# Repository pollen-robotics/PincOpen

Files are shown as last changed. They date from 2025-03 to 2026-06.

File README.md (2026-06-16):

[][cc-by-sa]

This work is licensed under a
[Creative Commons Attribution-ShareAlike 4.0 International License][cc-by-sa].

[][cc-by-sa]

[cc-by-sa]: http://creativecommons.org/licenses/by-sa/4.0/
[cc-by-sa-image]: https://licensebuttons.net/l/by-sa/4.0/88x31.png
[cc-by-sa-shield]: https://img.shields.io/badge/License-CC%20BY--SA%204.0-lightgrey.svg

Watch the video (https://www.youtube.com/shorts/5o2Au9_xjNQ)

# Pinc'Open project
[Pinc'Open](https://github.com/pollen-robotics/PincOpen/tree/main) is a low-cost (~25€) and open-source parallel-finger gripper, derived from [Pollen Robotics Reachy 2](https://www.pollen-robotics.com/reachy/)'s gripper

## Table of contents

- [Pinc'Open Presentation](#pincopen-project)
    - [What is Pinc'Open](#what-is-pincopen)
    - [Reachy 2 "Pincette" gripper](#reachy-2-pincette-gripper)
    - [Areas of focus](#areas-of-focus)
- [Build Resources](#build-resources)
    - [BOM (Bill Of Materials)](#bom-bill-of-materials)
    - [STL Files and Onshape document](#stl-files-and-onshape-document)
    - [Configure the motor before assembly](#configure-the-motor-before-assembly)
    - [Assembly Guide](#assembly-guide)
    - [How to flash and test the gripper](#how-to-flash-and-test-the-gripper)
- [Project Updates & Community](#project-updates--community)
    - [Updates history](#updates-history)
    - [Project posts](#project-posts)
    - [To Do List](#to-do-list)
    - [FAQ](#faq)
    - [Contact](#contact)
    - [Thank you](#thank-you)

## What is Pinc'Open?
The aim of this project is to make robotic manipulation more accessible, so that anyone with an idea but not the budget can make advances in this field possible.  
The quality of movement, mechanical strength and precision may not be as good as an industrial product, but a 2-finger parallel robotic gripper can be built for less than 25€! And we'll see that the performance is still good.  
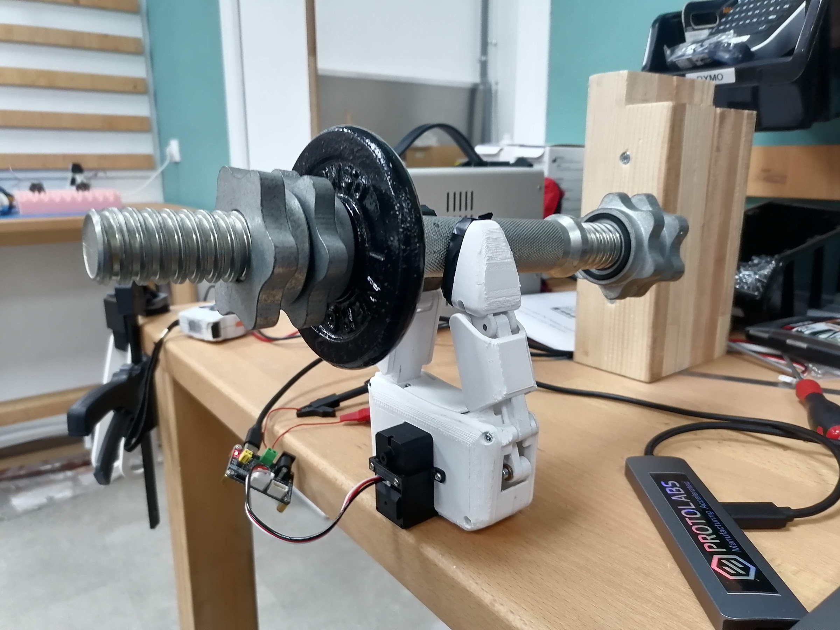
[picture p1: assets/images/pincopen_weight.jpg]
PincOpen_weight


The secondary goal is to make this gripper compatible with the [SO-ARM100](https://github.com/TheRobotStudio/SO-ARM100) open-source arm, so that the same motor as the current gripper can be used on our Pinc'Open. So the 25€ includes a motor that is already included in the $100 of the SO-ARM100.

What's more, the tip is interchangeable! That way, you can fit exactly what you need for your particular application.  
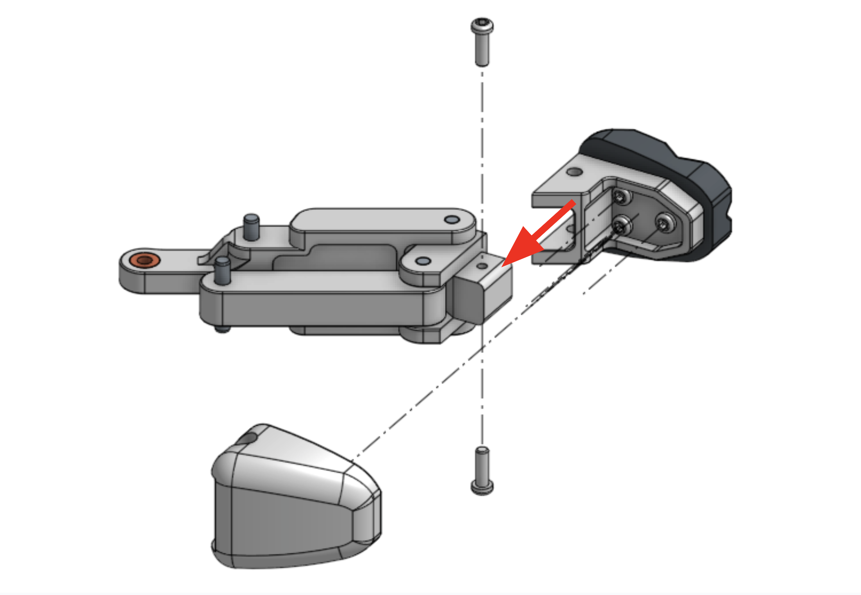
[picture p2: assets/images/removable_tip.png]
removable_tip


## Reachy 2 "Pincette" gripper
The Pincette v1.0 gripper, released at the same time as [Reachy 2](https://www.pollen-robotics.com/reachy/), is a two-parallel-finger hand designed for versatility and accurate, strong grasping.  
Pincette
Joints are based on high-quality standard components, and mechanical parts are machined from metal for greater rigidity and precision.  
However, these qualities come at a considerable cost: today, for just a few units manufactured, the BOM costs ~€1,700 per unit.  

This is acceptable depending on the application, but not for those who want to build a low-cost robotic gripper.

## Areas of focus:
- Make every mechanical custom part 3D printable, and not easily breakable, to avoid expensive metal machining.
- Change the expensive [Robotis Dynamixel motor](https://emanual.robotis.com/docs/en/dxl/x/xm430-w210/) to a cheap [Feetech STS3215](https://www.feetechrc.com/525603.html) motor.
- Remove all the high-quality but expensive standard components and find mechanical tricks to replace them.
- Find a trick to imitate a torque limitation while using position control on a motor that doesn't have this feature. Otherwise, the motor burns (or turns off thanks to security) or the plastic mechanical part can break...

# Build Resources
## BOM (Bill Of Materials)
The list of all needed components is available here:  
[PincOpen BOM](https://docs.google.com/spreadsheets/d/1iEKxfsqo3RnKw0QtdLJ2hEtYNDy2LInxrnCFLAhpxHk/edit?usp=sharing)  

There is the standalone PincOpen gripper BOM (~25€), then optional components like the interface with the [SO-ARM100](https://github.com/TheRobotStudio/SO-ARM100) project, or a Realsense camera stand for example.

## STL Files and Onshape document
STL and Steps files can be found [here](https://github.com/pollen-robotics/PincOpen/tree/main/cad)  

Everyone can access the Onshape document too:   
[Link Onshape](https://cad.onshape.com/documents/96518c699fd03eea508b06d3/w/d5f95a6266b027d84ae48634/e/e41e675b82a4f671f01336e0)  
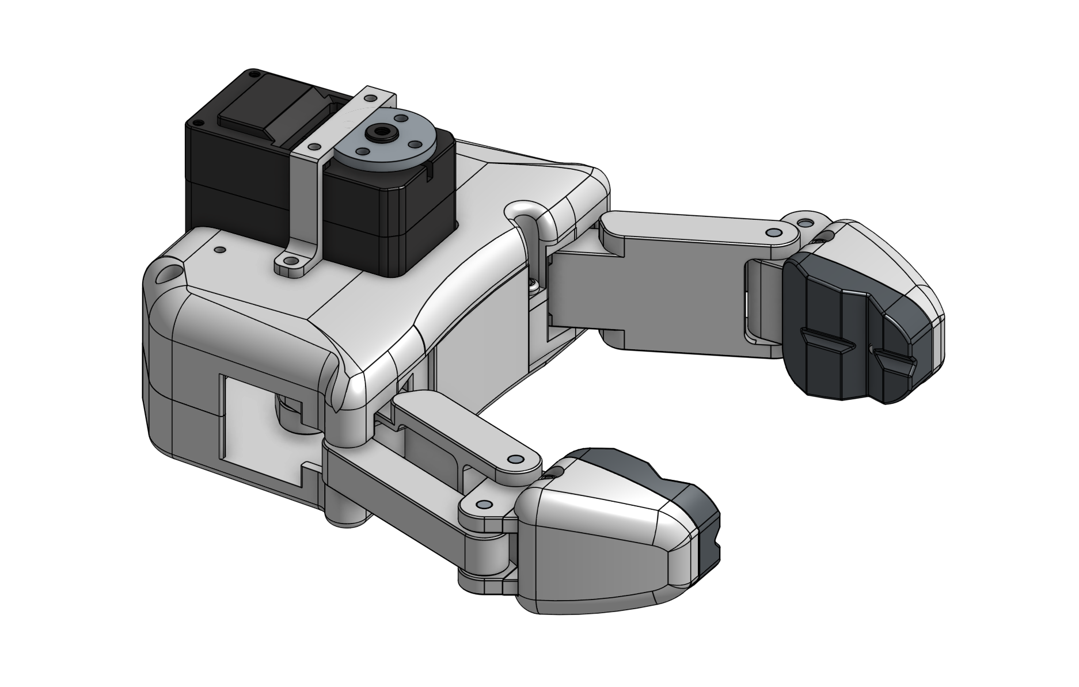
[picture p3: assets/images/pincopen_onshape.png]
pincopen onshape picture
  

Note that you can set a configuration in the assembly, like the default assembly, or with the interface part for SO-ARM100, or the configuration for camera mounting.

## Configure the motor before assembly
To configure the motor as it should be, please first clone & install [Lerobot library](https://github.com/huggingface/lerobot/tree/main).

Then connect and power up your motor, and run the following command: 

```bash
python lerobot/scripts/configure_motor.py --port /dev/ttyACM0 --brand feetech --model sts3215 --baudrate 1000000 --ID <ID>
```

Make sure to replace the port with your USB serial port and the ID with "6".

## Assembly Guide
Here is an assembly guide to explain how to print all the needed custom parts and how to use them to build this gripper.  
[=> Assembly Guide](/docs/PincOpen_Assembly_Instructions.pdf)  
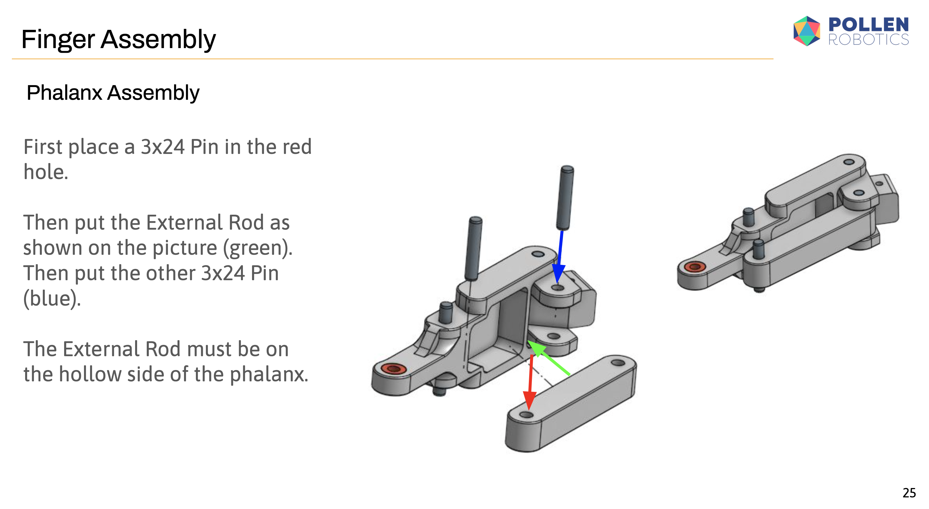
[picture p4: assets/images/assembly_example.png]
Assembly Example
  

There is also a guide about how to build an Intel Realsense D405 camera mount here:  
[=> Camera Mount Assembly](/docs/camera_mount_assemby.md)

## How to flash and test the gripper
First of all, please install the pypot library, updated with the Feetech motors:  
https://github.com/pollen-robotics/pypot/tree/support-feetech-sts3215  

Then, please refer to the [flash&test notebook](https://github.com/pollen-robotics/PincOpen/tree/main/flash_and_tests)

# Project Updates & Community
## Updates history
[Updates history](/docs/changelog.md)  

## Community projects
- ROS2 PincOpen Driver - School of Engineering and Computing, Christopher Newport University - [[Github](https://github.com/CNURobotics/pinc_open_driver)]. 
- MuJoCo Simulation Support (PR) - [[Github](https://github.com/pollen-robotics/PincOpen/pull/6)] 
- ICRA 2026 Smart grasping using embedded 3D force (tactile) sensing from Melexis - Milan Amighi, Constantin Scholz and Bram Vanderborght (Brubotics - VUB & imec), in collaboration with Melexis - [[Tutorial Website](https://mech.vub.ac.be/multibody/ICRA_conference_workshop.htm)]
- [Mobile Manipulation with LeKiwi and PincOpen](https://huggingface.co/blog/zuoxingdong/mobile-manipulation-lekiwi-pincopen) - Xingdong Zuo - [[Github](https://github.com/zuoxingdong/lerobot-lekiwi)]

## To Do List
- Video showing the advantages of this more complex mechanism
- Technical explanation about how it was designed
- New camera mounting supports

## Project posts
- [Fingertips for better grip](/docs/grip_tip.md)
- [Mobile Manipulation with LeKiwi and PincOpen](https://huggingface.co/blog/zuoxingdong/mobile-manipulation-lekiwi-pincopen) - Xingdong Zuo - [[Github](https://github.com/zuoxingdong/lerobot-lekiwi)]

## FAQ
WIP

## Contact
[Contact me or Pollen Robotics](/docs/contact.md)

## Thank you
Huge thanks to those who have contributed to this project so far:
- [Antoine Pirrone](https://github.com/apirrone) for making great demos, all the advice and feedback
- [Pierre Rouanet](https://github.com/pierre-rouanet) for Feetech motors integration in pypot  
- [Jeremy Laville](https://www.linkedin.com/in/jeremy-laville-1038b176/) & [Matthieu Lapeyre](https://www.linkedin.com/in/matthieulapeyre/) for mechanical advice and original Reachy 2 Pincette co-development

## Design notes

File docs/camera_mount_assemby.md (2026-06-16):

# On-wrist Camera Mount Assembly

1. With a soldering iron, place 2x M3 inserts here:
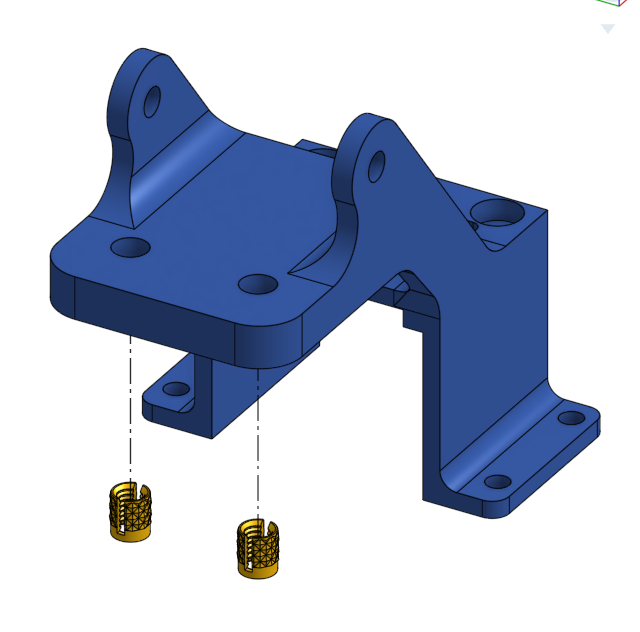
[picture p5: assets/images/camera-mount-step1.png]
Step 1
 

2. Then place 2x M3x25 screws here, used to adjust the angle of the camera, plus 2 nuts to lock the screw positions:
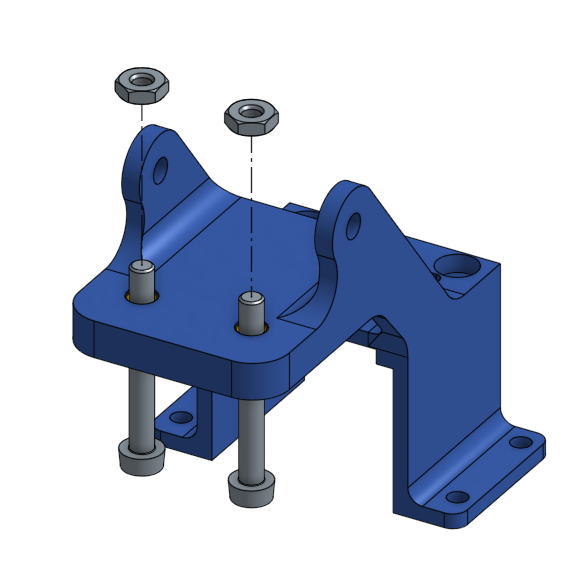
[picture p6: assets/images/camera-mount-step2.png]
Step 2


3. Put the mobile support in the base and secure the axis with two self-tapping 3x8mm screws (thermoplastic screws):
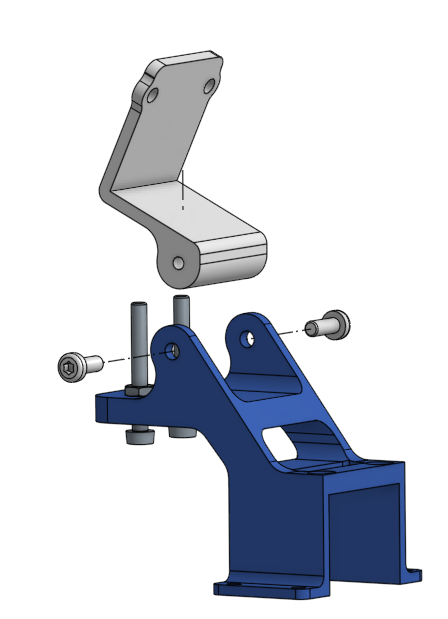
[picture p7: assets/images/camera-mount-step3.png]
Step 3


4. Then place the camera's back holes in front of the holes of the mobile support part and put in 2x M3x6 screws:
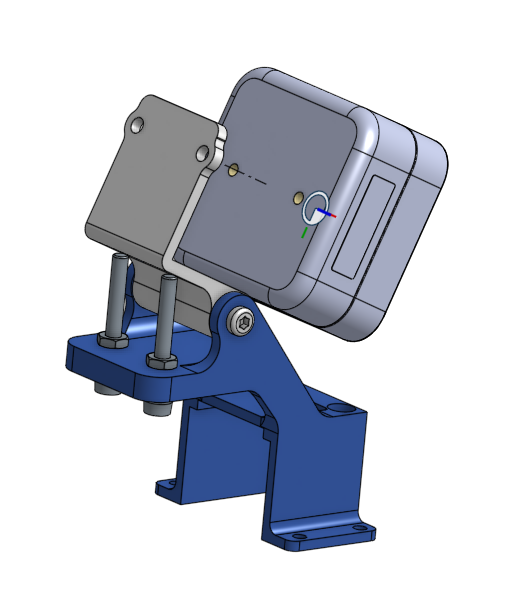
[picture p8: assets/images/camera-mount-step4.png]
Step 4


5. Put in 4x self-tapping 2.5x6mm screws:
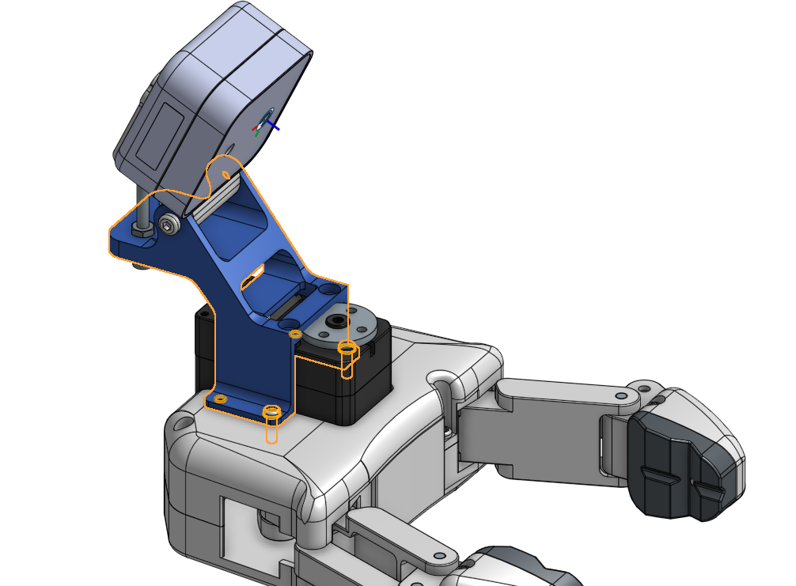
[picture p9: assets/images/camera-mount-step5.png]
Step 5


*Thanks to [Xingdong Zuo](https://github.com/zuoxingdong) for the contribution of this camera mount assembly guide.*

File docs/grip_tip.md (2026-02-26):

## Fingertips for Better Grip

We've added a small but useful feature to the fingertip design in the [Onshape model](https://cad.onshape.com/documents/96518c699fd03eea508b06d3/w/d5f95a6266b027d84ae48634/e/e41e675b82a4f671f01336e0), making it easier to improve grip performance.

### Flat Tip Design for Adhesive Grip Layers

The tip of the finger can be **flattened**, allowing you to:
- Cut the same shape from the **adhesive or anti-slip material** of your choice
- Stick it onto the fingertip
- **Fold the side flaps** neatly around the edges

To secure the folded flaps in place, you can add a **thin strip of tape or band** around the perimeter of the tip. This helps maintain a clean and durable finish.

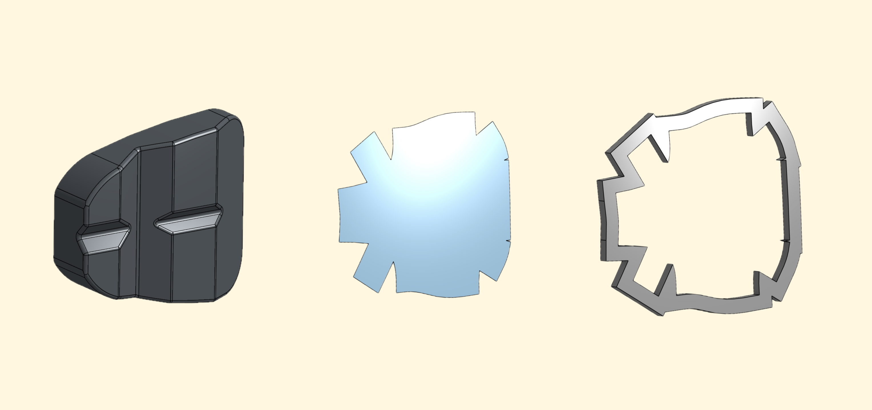
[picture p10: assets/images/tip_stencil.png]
tip_stencil


### Best Performing Material So Far: **3M GM400**

After testing various grip-enhancing materials, our favorite so far is the **3M GM400**

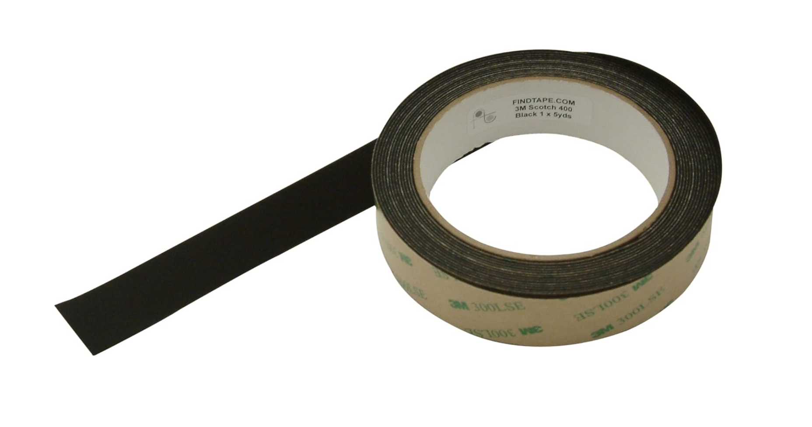
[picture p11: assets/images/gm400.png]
gm400


- Strong **dry adhesion** (not sticky, but highly grippy)
- Excellent **friction**, even on smooth objects
- Durable and **wear-resistant**, sticks well
- Easy to cut and apply

However, the cost is quite high and the quantity is probably too much for just covering one gripper tip...

> ⚠️ _Note: We have **no affiliation with 3M** — this is an objective recommendation based on hands-on testing._

### TPU Option – Deformable but Solid

You can also 3D print the fingertips in **TPU** with a **moderate infill (30–50%)**, resulting in:
- A flexible structure that adapts to object shapes
- Enough rigidity to preserve form and control

Combining TPU with an adhesive grip layer offers a great balance between **compliance and friction**.

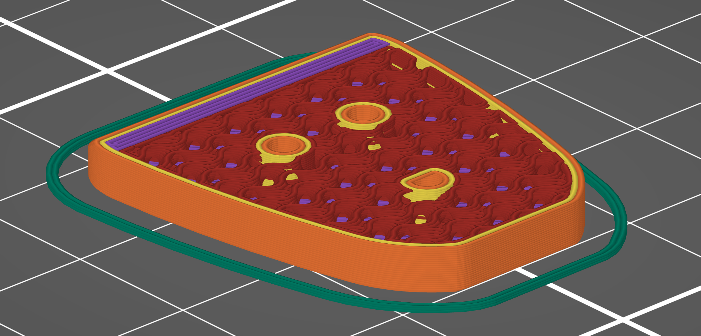
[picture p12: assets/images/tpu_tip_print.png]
tpu_tip


### Personal Preference: Rigid Base + Grip Layer

While TPU works well, **our personal preference** is to use a **rigid tip (PLA or PETG)** and simply add a **thin rubber-like or anti-slip layer** (such as GM400) on top.  
This approach avoids unwanted deformation, while still ensuring **strong and reliable grip** — especially useful when precise, repeatable grasps are needed.

Feel free to experiment with different grip materials — the flat tip shape makes it easy to try out and swap alternatives depending on your use case or your budget.

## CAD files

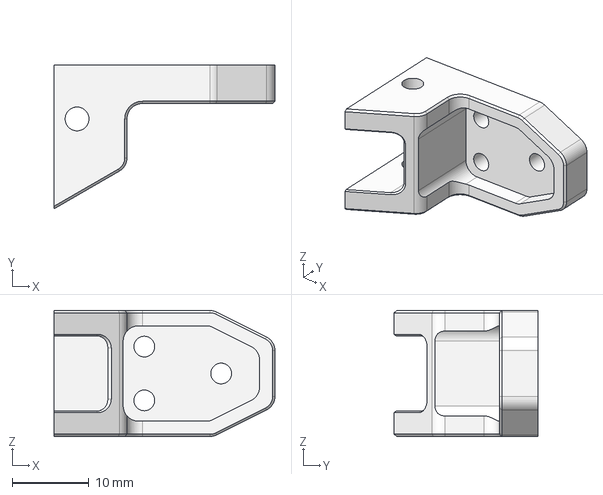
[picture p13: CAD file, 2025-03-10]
cad/step/Removable_Tip.step
28.8 x 18.7 x 16.4 mm

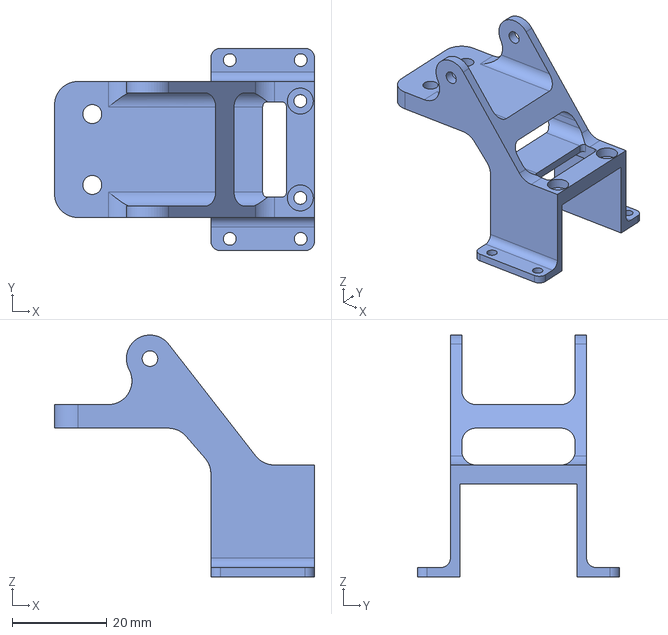
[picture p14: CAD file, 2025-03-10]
cad/step/Camera_basement.step
55.0 x 42.8 x 51.2 mm

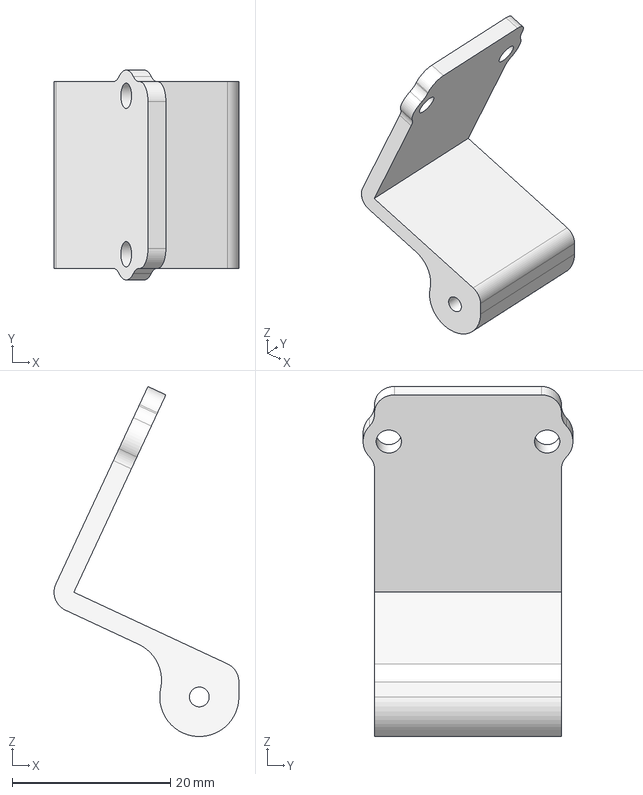
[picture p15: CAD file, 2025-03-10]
cad/step/Camera_mobile_sup.step
23.3 x 26.5 x 44.2 mm

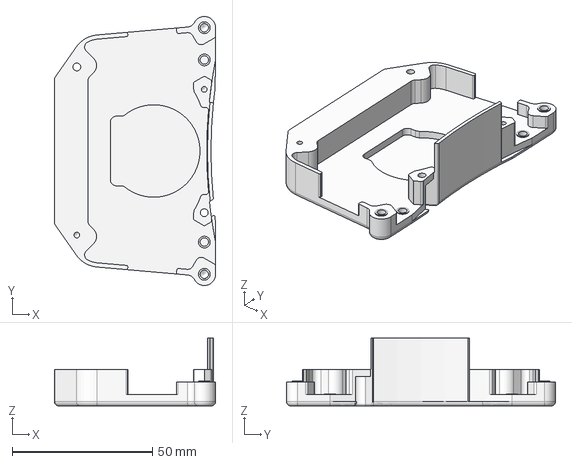
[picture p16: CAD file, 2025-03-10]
cad/step/Bottom_Plate.step
57.5 x 96.0 x 24.2 mm

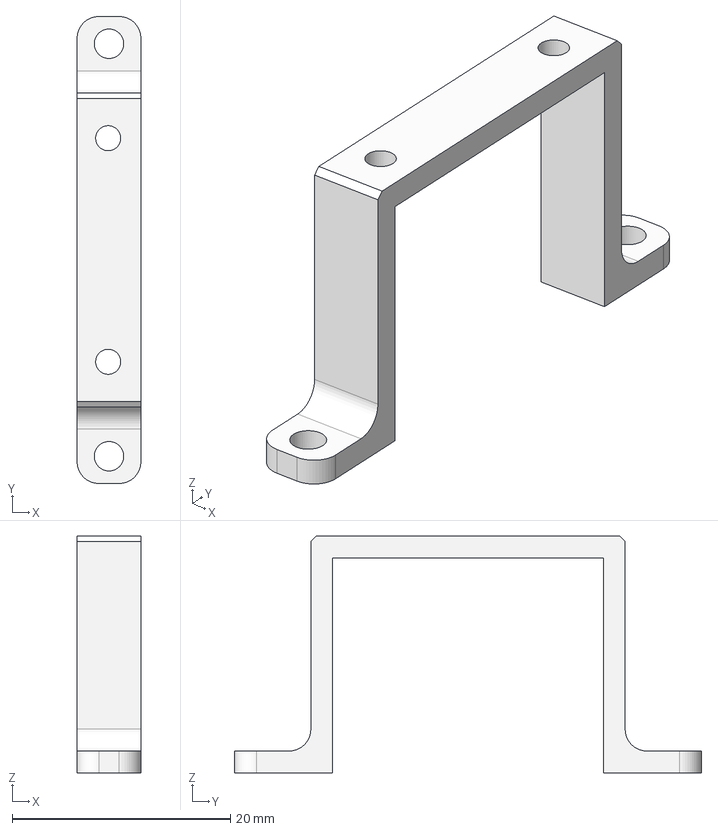
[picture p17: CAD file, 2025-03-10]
cad/step/Motor_Flange.step
5.85 x 42.8 x 21.7 mm

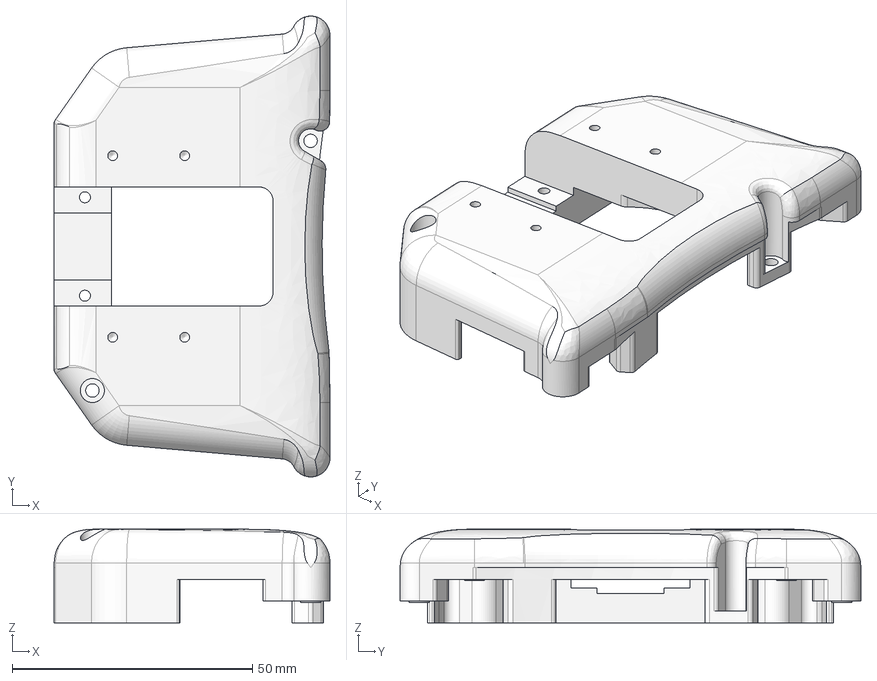
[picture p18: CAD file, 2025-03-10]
cad/step/Top_Plate.step
57.5 x 96.0 x 19.5 mm

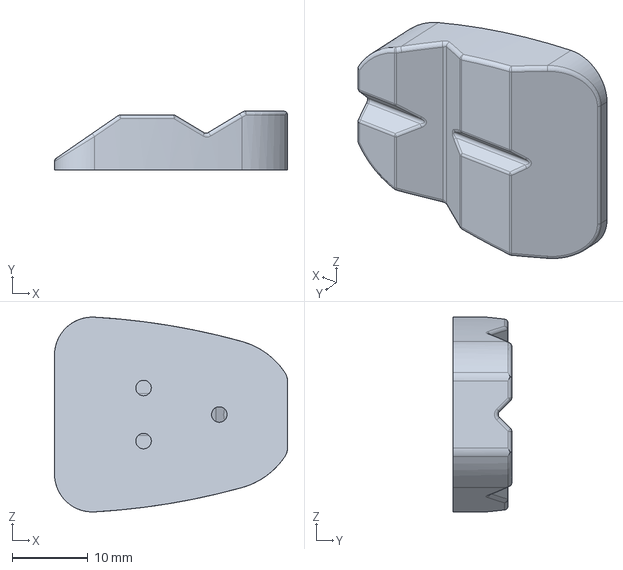
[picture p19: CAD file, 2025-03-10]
cad/step/Tip_Support.step
30.8 x 7.75 x 25.7 mm

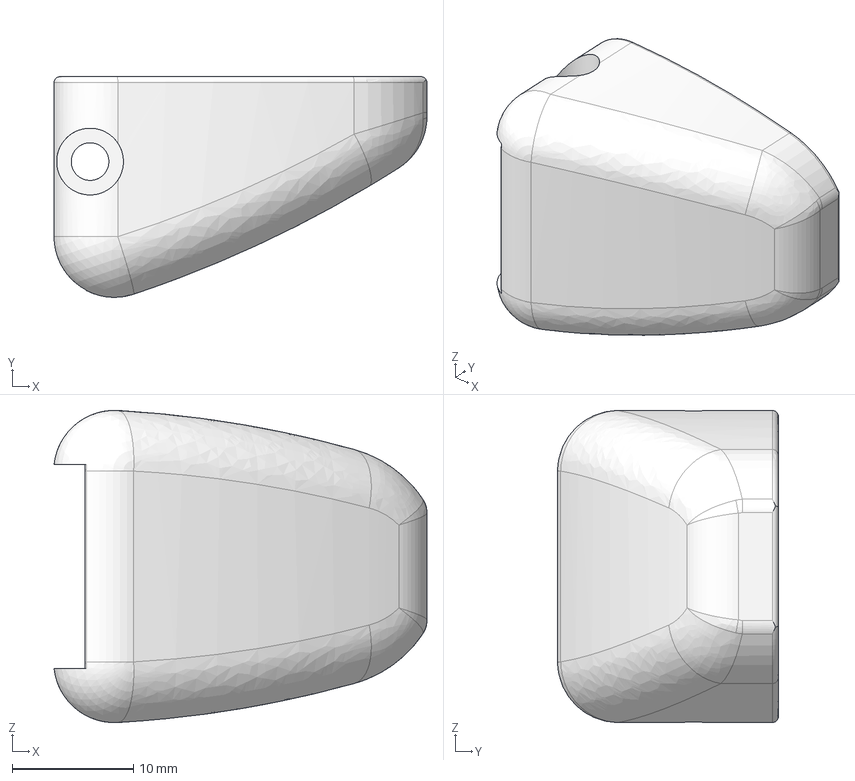
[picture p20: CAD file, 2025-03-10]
cad/step/Distal_Shell.step
30.7 x 18.2 x 25.7 mm

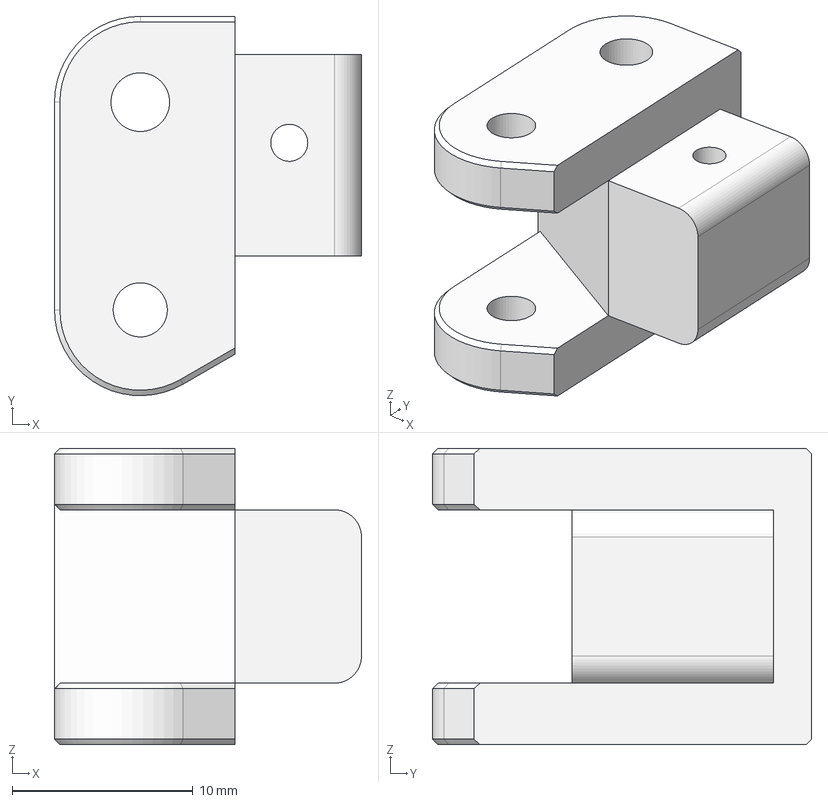
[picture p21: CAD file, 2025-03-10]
cad/step/Distal_Rod.step
17.0 x 21.0 x 16.4 mm

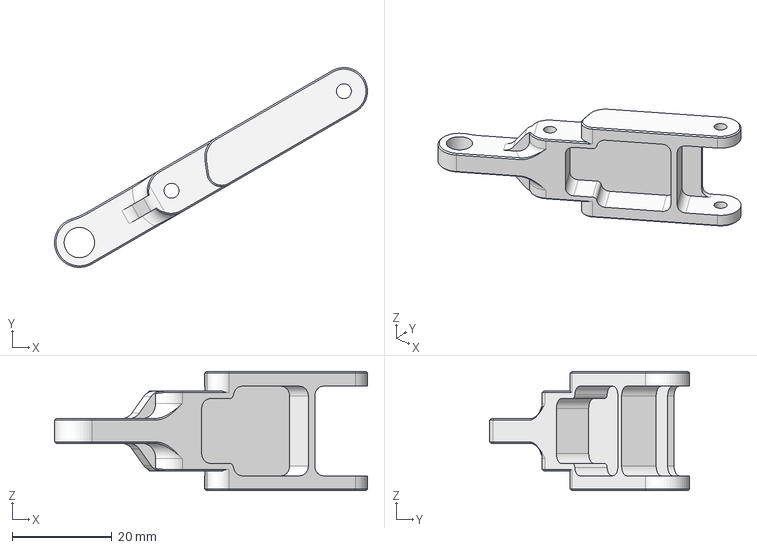
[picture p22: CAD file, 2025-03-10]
cad/step/Internal_Rod.step
62.9 x 40.2 x 24.0 mm

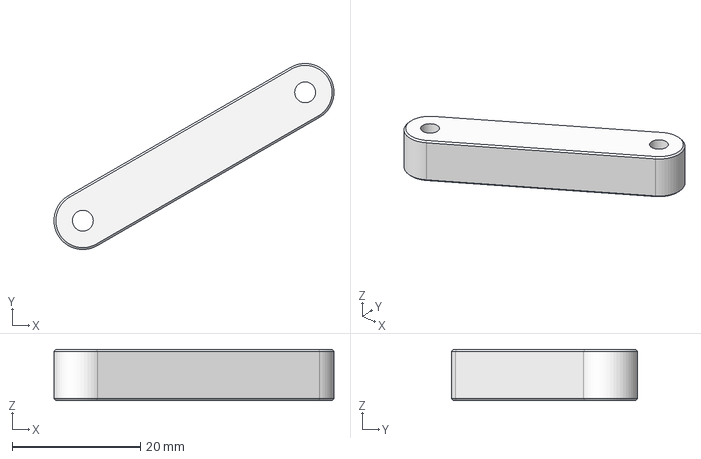
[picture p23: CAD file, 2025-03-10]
cad/step/External_Rod.step
43.6 x 29.0 x 8.00 mm

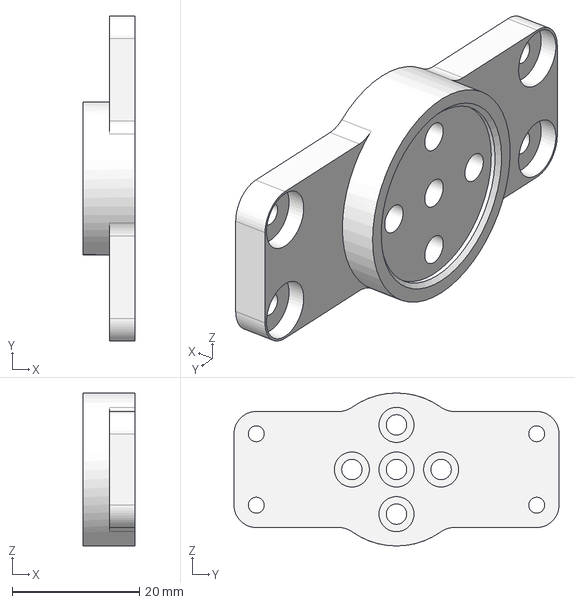
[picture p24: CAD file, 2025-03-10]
cad/step/Interface_ARM100.step
8.12 x 51.0 x 24.0 mm

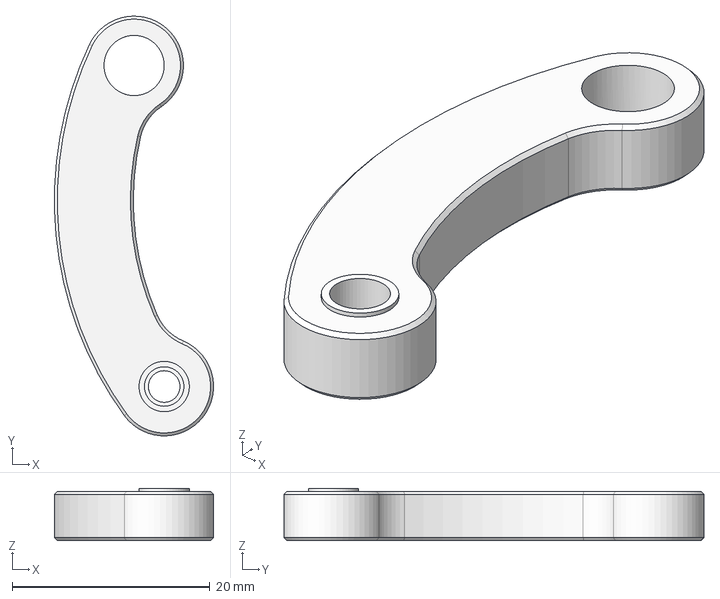
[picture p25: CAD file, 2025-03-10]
cad/step/Driving_Rod.step
16.1 x 42.5 x 5.30 mm

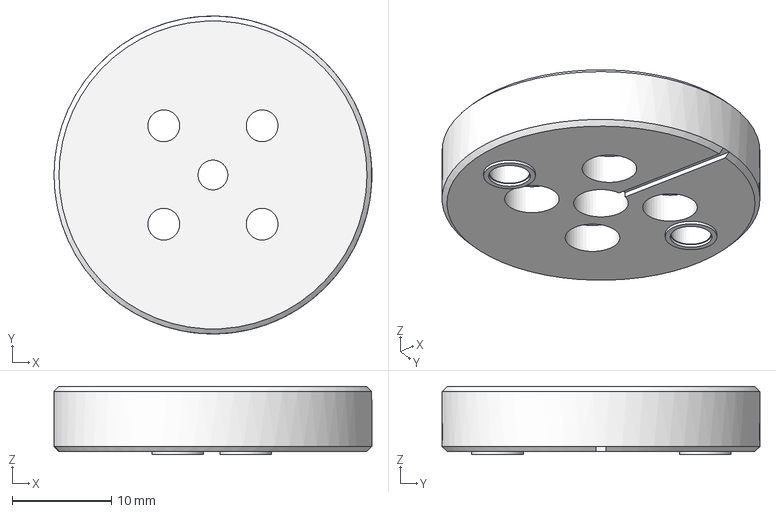
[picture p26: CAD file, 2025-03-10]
cad/step/Cam.step
32.0 x 32.0 x 6.85 mm

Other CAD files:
cad/stl/Bottom_Plate.stl
cad/stl/Cam.stl
cad/stl/Camera_basement.stl
cad/stl/Camera_mobile_sup.stl
cad/stl/Distal_Rod.stl
cad/stl/Distal_Shell.stl
cad/stl/Driving_Rod.stl
cad/stl/External_Rod.stl
cad/stl/Interface_ARM100.stl
cad/stl/Internal_Rod.stl
cad/stl/Motor_Flange.stl
cad/stl/Removable_Tip.stl
cad/stl/Tip_Support.stl
cad/stl/Top_Plate.stl

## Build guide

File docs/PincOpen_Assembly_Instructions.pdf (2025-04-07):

Augustin Crampette
augustin.crampette@pollen-robotics.com or contact@pollen-robotics.com
Pollen Robotics
Bordeaux, France

# Pinc’ Open

### Gripper low cost & open source

### Assembly Guide - v1.2

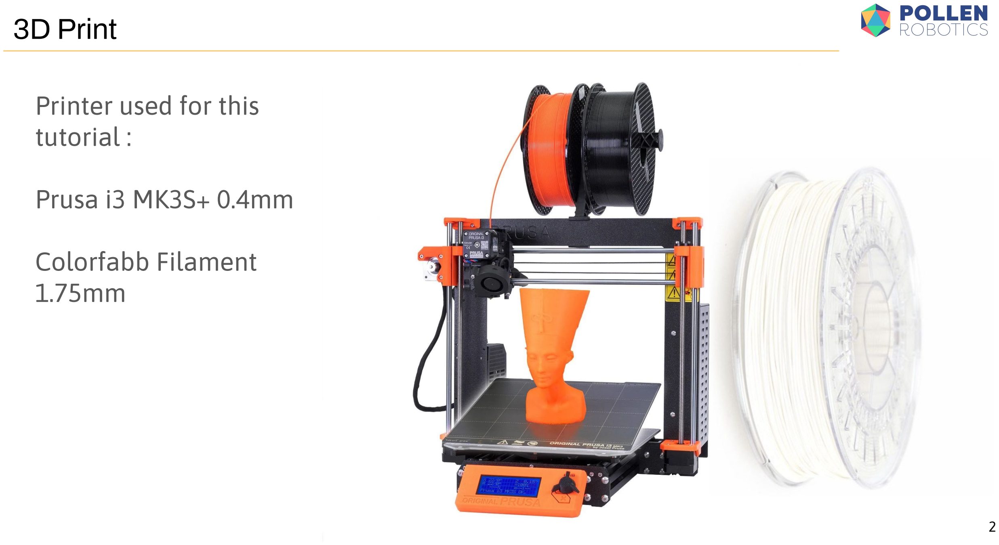
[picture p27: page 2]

### 3D Print

Printer used for this
tutorial :

Prusa i3 MK3S+ 0.4mm

Colorfabb Filament
1.75mm

### 3D Print - 20% infill & Support on build plate only

PincOpen - Bottom_Plate

### 3D Print - 20% infill & Support on build plate only

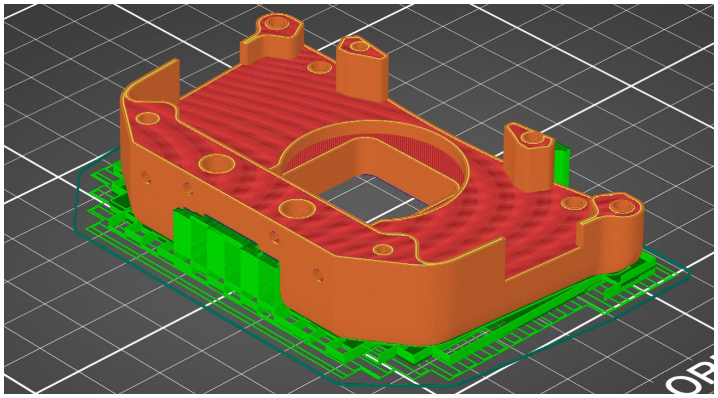
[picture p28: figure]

PincOpen - Top_Plate

### 3D Print - 20% infill & Support on build plate only

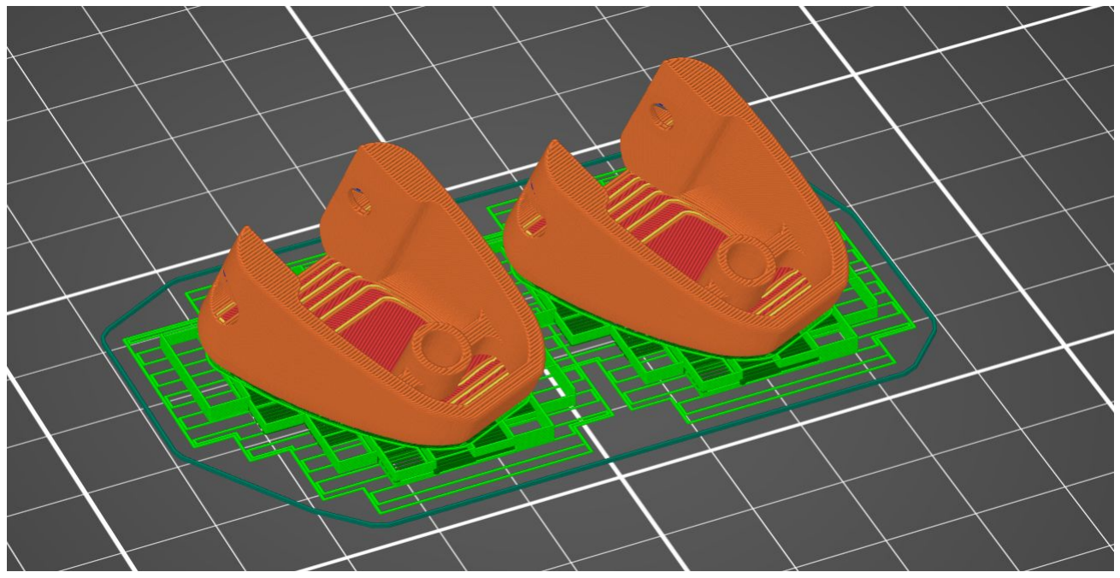
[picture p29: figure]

PincOpen - Distal_shell

### 3D Print - 20% infill & Support on build plate only

PincOpen - Motor_flange

### 3D Print - 20% infill & Support on build plate only

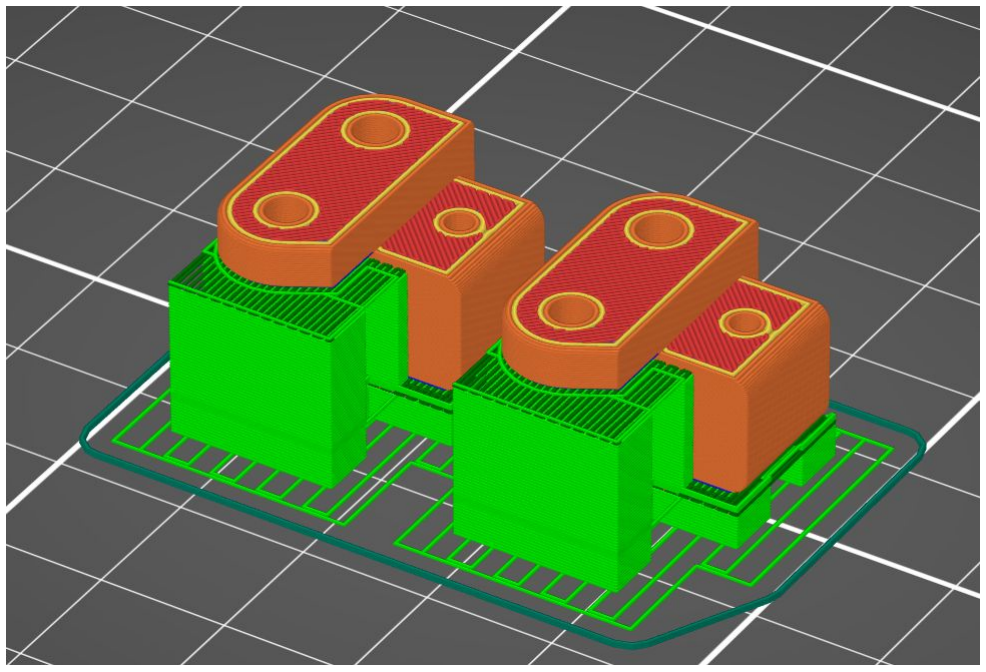
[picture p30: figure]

PincOpen - Distal_Rod
Supports will be a bit tricky to remove, but necessary to have nice circular holes.

### 3D Print - 20% infill & No Support

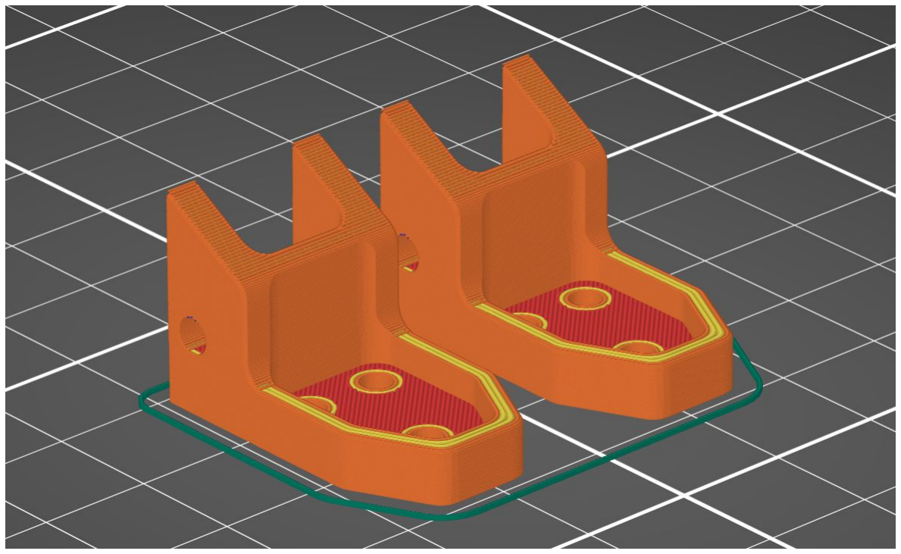
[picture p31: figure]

PincOpen - Removable_Tip

### 3D Print - 20% infill & No Support

PincOpen - Tip_Support

### 3D Print - 20% infill & No Support

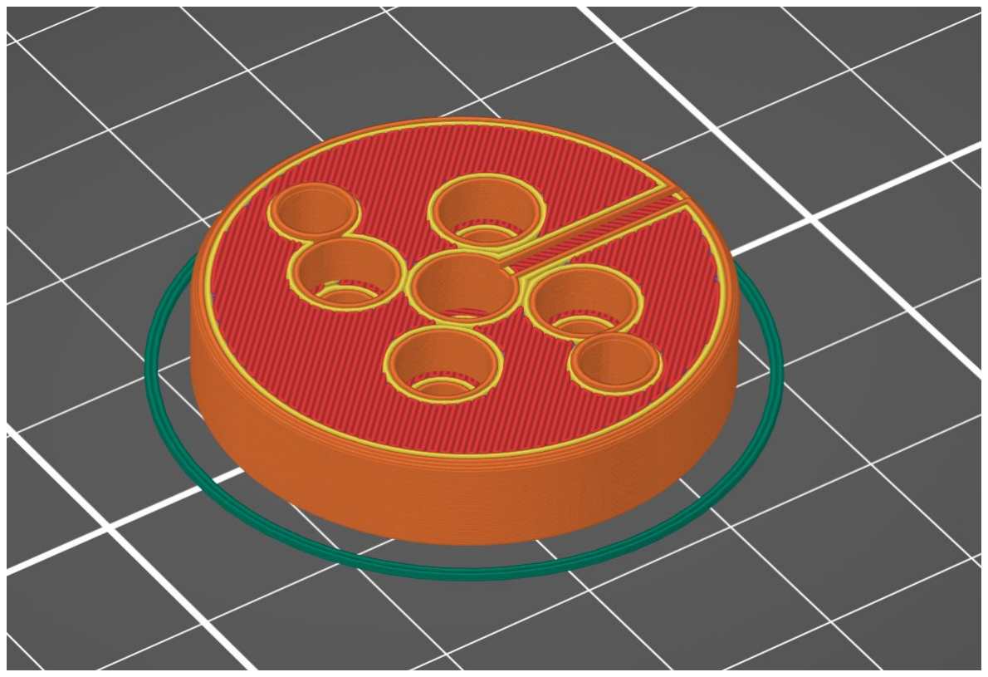
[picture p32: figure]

PincOpen - Cam

### 3D Print - 20% infill & No Support

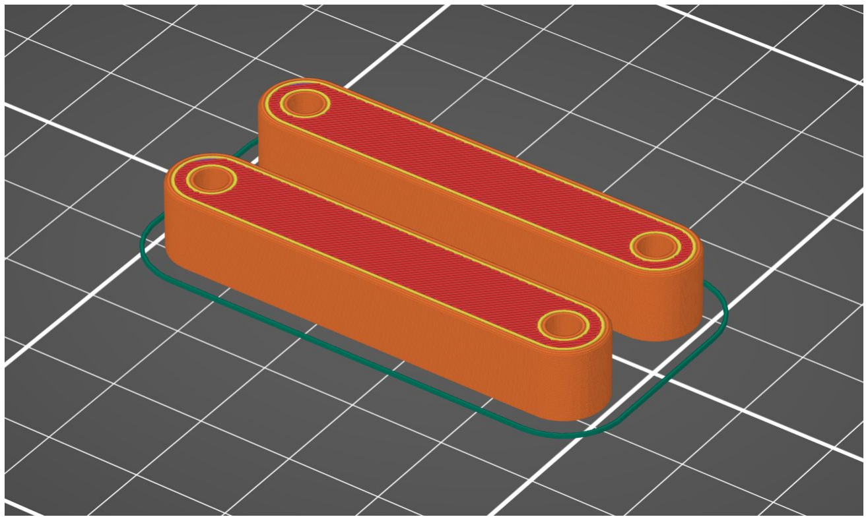
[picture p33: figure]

PincOpen - External_Rod

### 3D Print - 80% infill & No Support

PincOpen - Driving_Rod

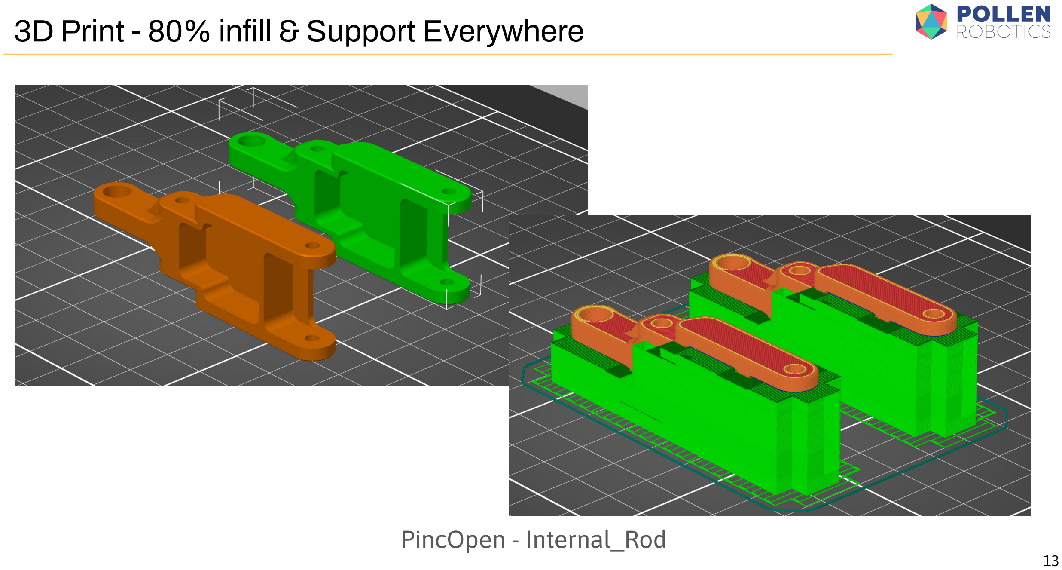
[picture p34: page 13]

### 3D Print - 80% infill & Support Everywhere

PincOpen - Internal_Rod

### Material Preparation

Tools - Several Phillips

screwdrivers
- Small Flat Screwdriver - Files & 3mm drill - Cutter - Strong Glue - Adjustable Pliers - (optional) Chatterton

Tape
- (optional) Loctite 243 & 648

### Material Preparation

Custom Parts 2x PP008 Removable Tip 2x PP010 Distal Shell

2x PP004 Internal Rod

2x PP006 Distal Rod | 2x PP005 External Rod

1x PP002 Cam

1x PP001 Top Plate

1x PP003 Bottom Plate 2x PP009 Tip Support | 1x PP011 Motor Flange

2x PP007 Driving Rod

### Material Preparation

### Standard Parts

4x STD003 Pin 3 x 16 (h6) 4x STD004 Pin 3 x 24 (h6)

20x STD005 Thermoplastic Screw
| 2.5x8 mm
1x STD001 Feetech STS3215

4x STD006 plain bearing
3x6x5 mm

4x STD008 Brass Inserts

4x Screws M3x0.5x10

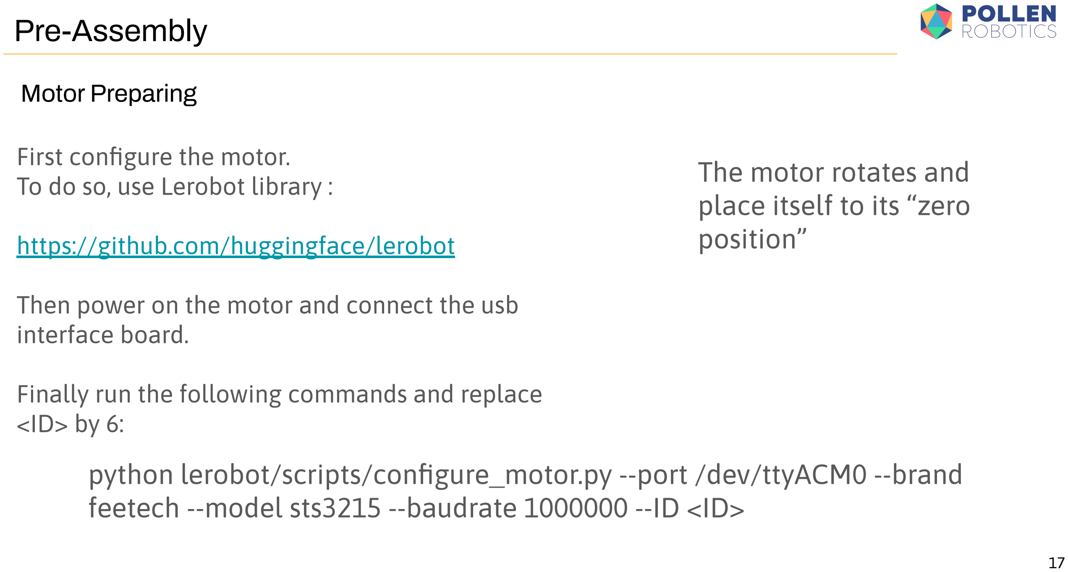
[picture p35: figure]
Pre-Assembly; Motor Preparing; https://github.com/huggingface/lerobot; interface board.; The motor rotates and place itself to its “zero position”

First configure the motor. To do so, use Lerobot library :

Then power on the motor and connect the usb

Finally run the following commands and replace

python lerobot/scripts/configure_motor.py --port /dev/ttyACM0 --brand feetech --model sts3215 --baudrate 1000000 --ID <ID>

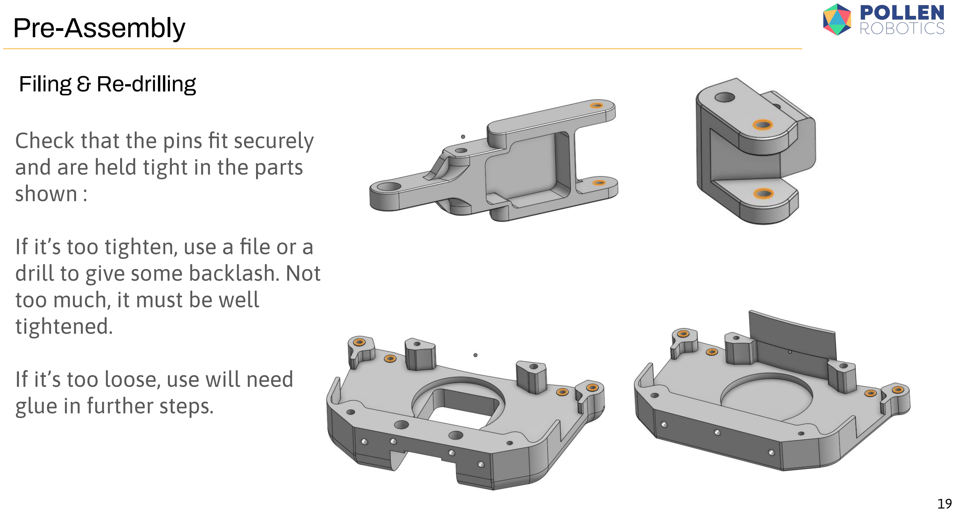
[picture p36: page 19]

### Pre-Assembly

Filing & Re-drilling

Check that the pins fit securely and are held tight in the parts shown :

If it’s too tighten, use a file or a drill to give some backlash. Not too much, it must be well
tightened.

If it’s too loose, use will need glue in further steps.

### Pre-Assembly

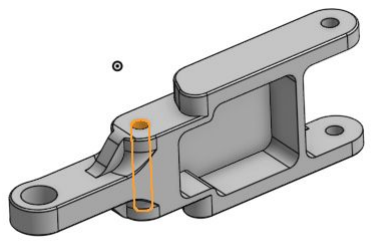
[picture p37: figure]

Filing & Re-drilling

Check that the pins fit and rotate easily and are not held in the parts shown :
If it’s not loose enough, use a drill.

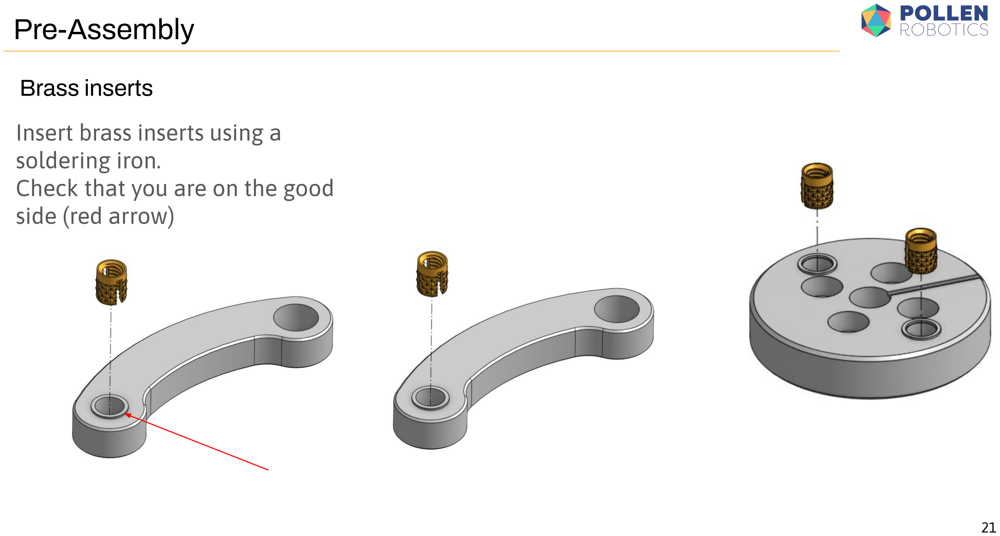
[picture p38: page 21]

### Pre-Assembly

Brass inserts
Insert brass inserts using a soldering iron.
Check that you are on the good side (red arrow)

### Pre-Assembly

Insert the bearings in the bores provided

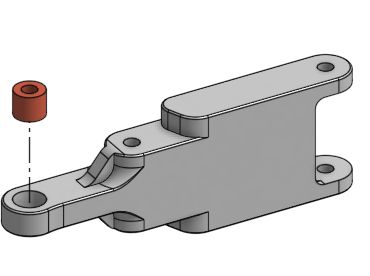
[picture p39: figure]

The bearing is supposed to fit
by forcing with hand, or pressed
onto a solid surface.
No tool is needed here.

If it’s to hard, file or drill the hole a bit and repeat so that it fits tighten.

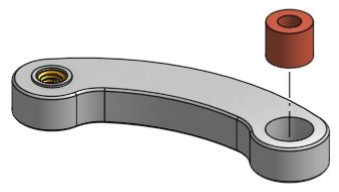
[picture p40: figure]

If the hole is too wide, put a drop of glue.

### Finger Assembly

Tip Assembly

Use 3x 2.5x8 Thermo screws To fasten the tip on the distal rod

Then just press the shell on the assembly.
It will be securely attached later.

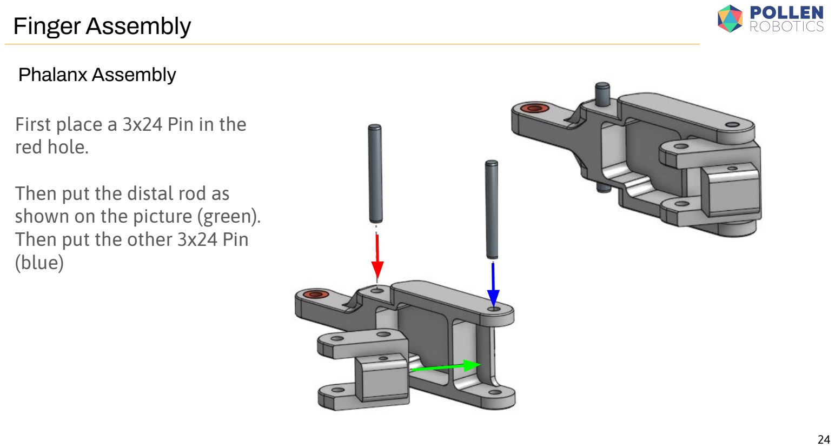
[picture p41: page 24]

### Finger Assembly

Phalanx Assembly

First place a 3x24 Pin in the red hole.

Then put the distal rod as shown on the picture (green). Then put the other 3x24 Pin (blue)

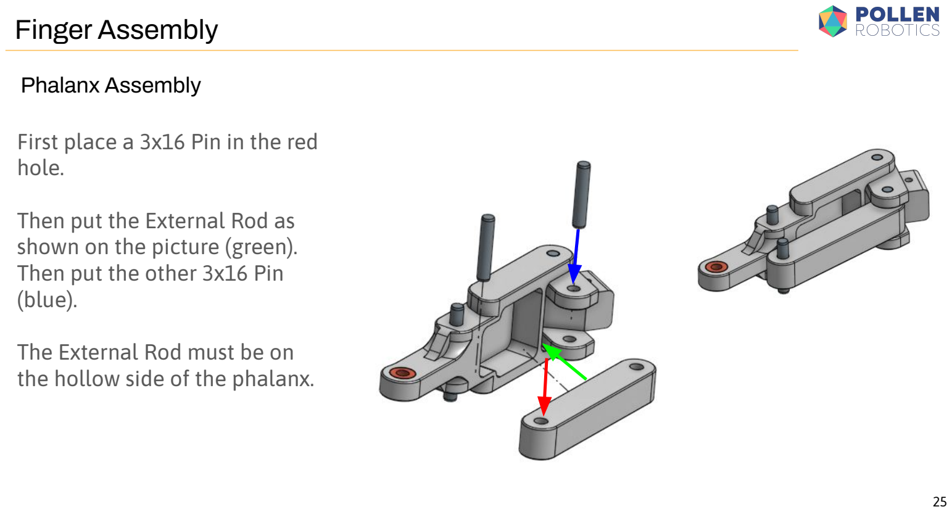
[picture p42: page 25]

### Finger Assembly

Phalanx Assembly

First place a 3x16 Pin in the red hole.

Then put the External Rod as shown on the picture (green). Then put the other 3x16 Pin (blue).

The External Rod must be on the hollow side of the phalanx.

### Finger Assembly

Phalanx Assembly
Remove the shell.
Insert the pre-assembled tip on the dovetail (Red Arrow)

Then replace the shell and tighten 2x Thermoplastic
2.5x8mm Screws

### Finger Assembly

Right Finger

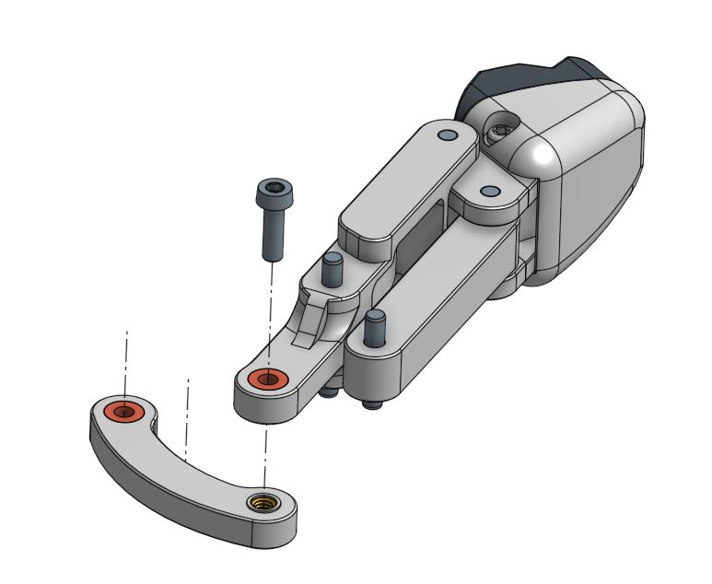
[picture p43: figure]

For the right finger, the Driving Rod must be place as shown on the picture.

Use a M3x0.5x10 screw to
tighten them and put some
loctite 648 to lock it.
It should be free to rotate don’t tighten it too much. The loctite secures it.

(You can use strong glue if you don’t have loctite 648.)

### Finger Assembly

Left Finger

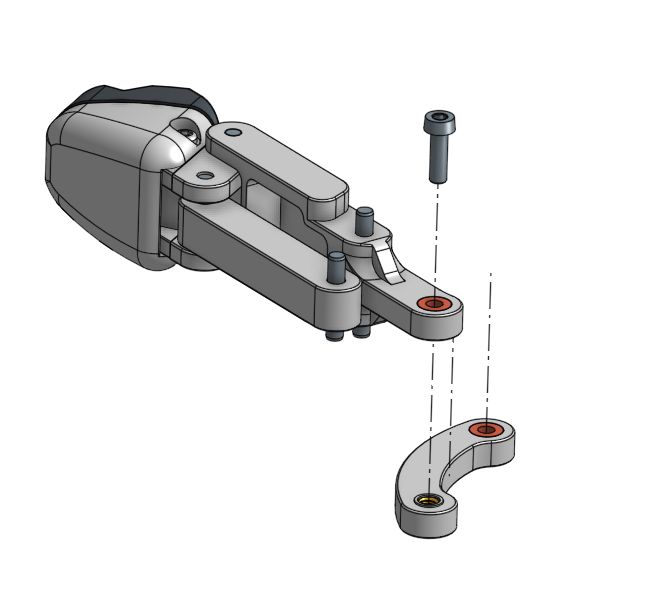
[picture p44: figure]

For the leftt finger, the Driving Rod must be place as shown on the picture.

Use a M3x0.5x10 screw to
tighten them and put some
loctite 648 to lock it.
It should be free to rotate don’t tighten it too much. The loctite secures it.

(You can use strong glue if you don’t have loctite 648.)

### Finger Assembly

Both Fingers

You left and right fingers must look like this:

Left
Right

### Palm Assembly

Motor Flange

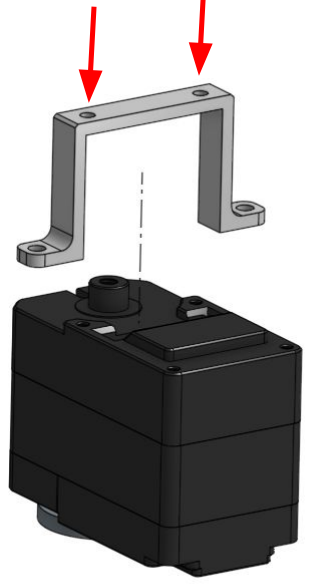
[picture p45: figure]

Use the self-tappping screws provided by Feetech to fix the flange on the motor.

### Palm Assembly

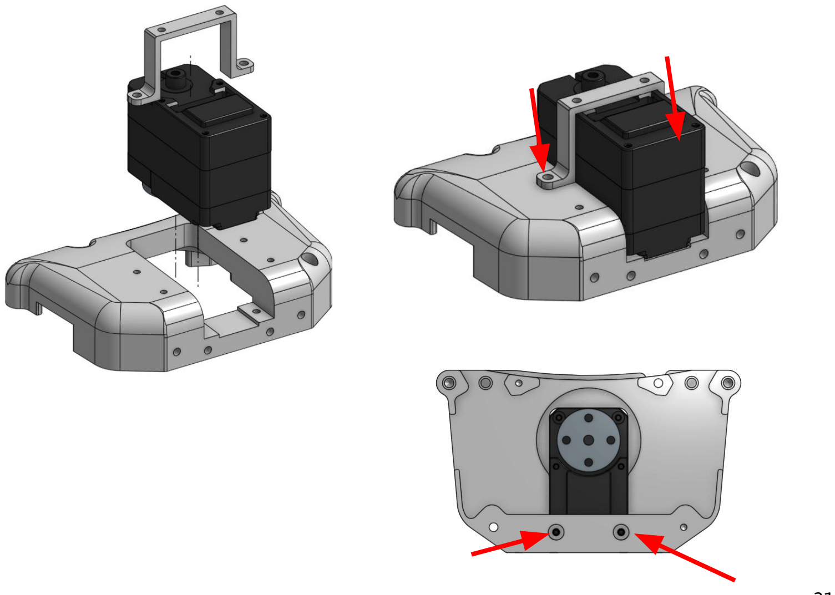
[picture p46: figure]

Motor on palm

Put the motor in its slot on the palm. You shouldn’t have to force much.

Then use 2x thermoplastic
2.5x8mm screws but don’t
tighten them.

Finally put 2x Feetech
self-tapping screws as indicated on the last picture.
Tighten them well, then tighten the first 2x screws on the top.

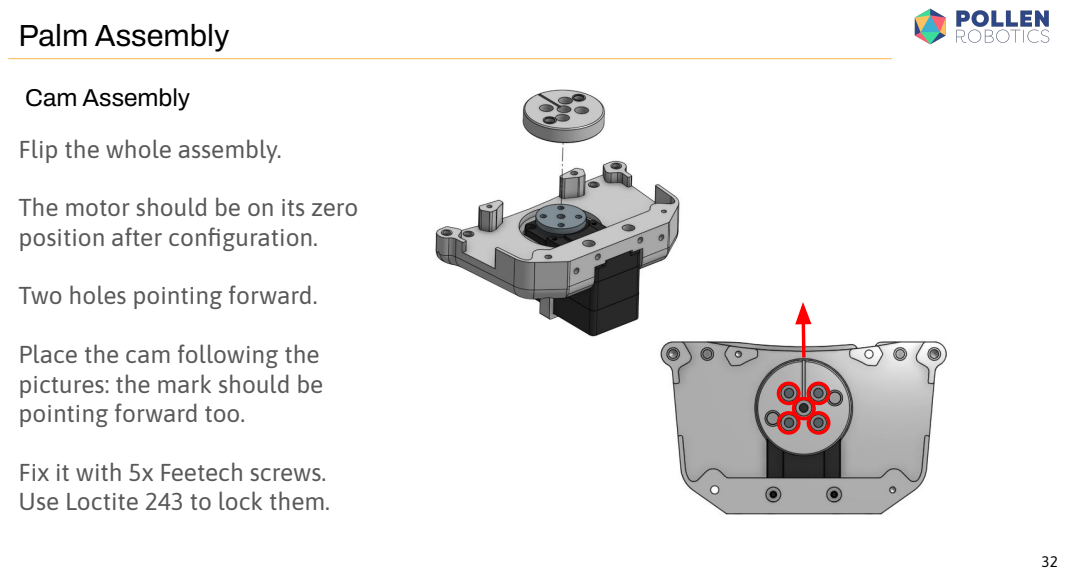
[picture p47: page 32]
Palm Assembly

Cam Assembly
Flip the whole assembly.

The motor should be on its zero
position after configuration.

Two holes pointing forward.

Place the cam following the
pictures: the mark should be
pointing forward too.

Fix it with 5x Feetech screws.
Use Loctite 243 to lock them.

### Palm Assembly

Right Finger
As the assembly is flipped, the right finger is flipped too and on our left now.

Insert in the indicated holes the 3mm pins.
Adjustable pliers can be used to help fitting the pins in the holes strongly.

Use a M3x0.5x10 screws and loctite 648 (or glue) to tighten the driving rod on the cam.
It should be free to rotate, don’t tighten too much. the glue secures it.

Flipped Right Finger

### Palm Assembly

Left Finger

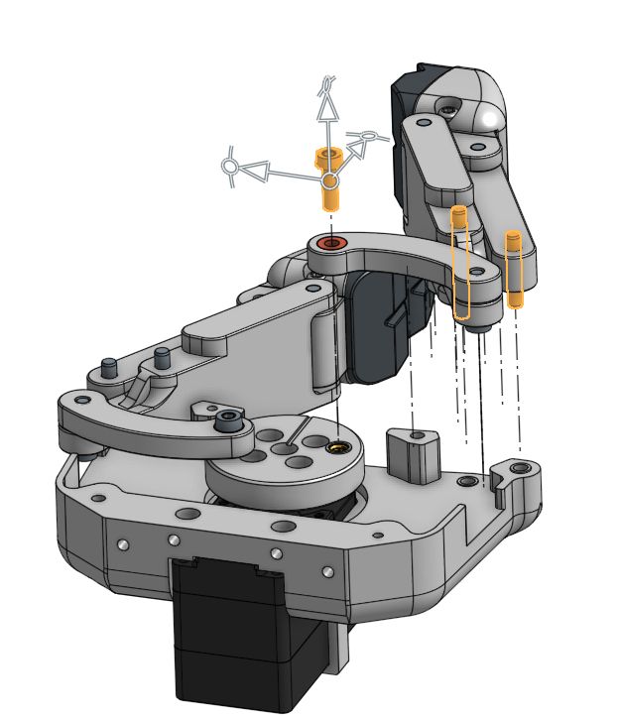
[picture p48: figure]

Repeat the last step for the flipped left finger.

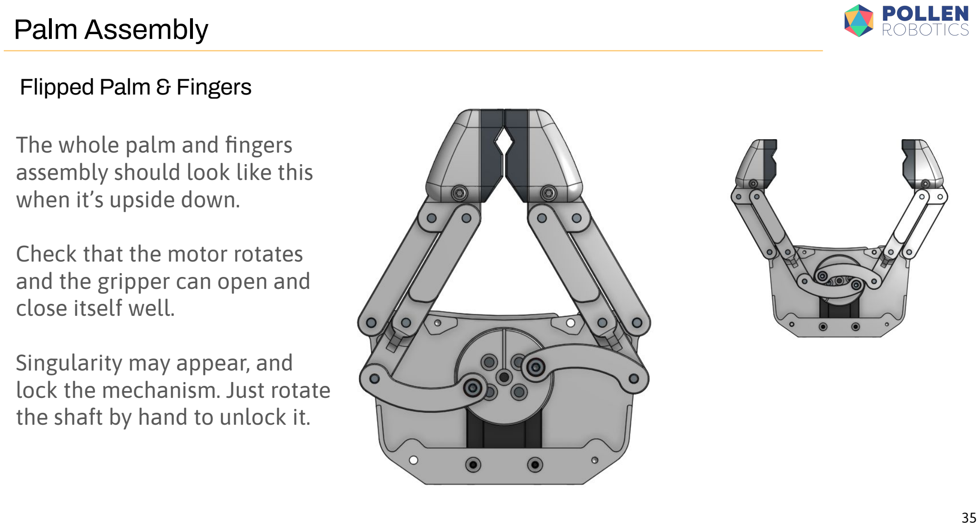
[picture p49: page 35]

### Palm Assembly

Flipped Palm & Fingers

The whole palm and fingers assembly should look like this when it’s upside down.

Check that the motor rotates and the gripper can open and close itself well.

Singularity may appear, and lock the mechanism. Just rotate the shaft by hand to unlock it.

### Palm Assembly

Shell closing

Use 4x 2.5x8 Thermo screws To close the palm with the bottom plate.

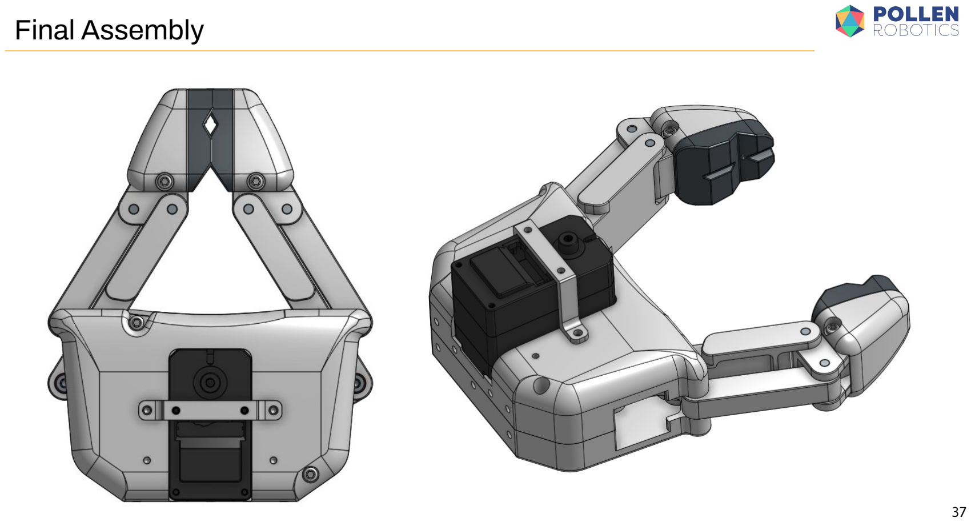
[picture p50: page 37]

### Final Assembly

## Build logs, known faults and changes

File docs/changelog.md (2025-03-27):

# Updates history

## v1.0 - 10/03/2025
- Publish the project
- Includes BOM, Assembly guide etc...

## v1.0 - 27/03/2025
### Added
- Stencil on Onshape to cut a rubber/tape cover for the tips
- New post added : **Fingertips for Better Grip**

### Fixed
- BoM mistakes

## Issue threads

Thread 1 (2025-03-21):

Mismatch in STD005 Thermoplastic Screw between Assembly Instructions and BOM

tc-huang, 2025-03-21:
Hello,

Thank you for creating such a fantastic project!

I noticed that the `PincOpen_Assembly_Instructions.pdf` specifies the `STD005` thermoplastic screw as `2.5x6 mm`, while the `BOM_PincOpen` Google Form lists it as `M2.5x8`. The attached screenshots show these discrepancies.

Since this is my first time handling screw specifications, I'm not sure if I've misunderstood something. Could you please clarify which specification is correct?

Thank you in advance!

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

augustin-crampette, 2025-03-21:
Hi!
Thank you for you issue.
There was a mistake in the BOM and Assembly about these screws. I just fixed the BOM and Assembly Instructions!
You only need 2.5x8mm thermoplastic screws, no 2.5x6mm :)

tc-huang, 2025-03-21:
Hi @augustin-crampette

Thanks for the quick reply! I'm glad I could help!

Closed 2025-03-21.

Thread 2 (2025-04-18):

Mounted camera support

alexcbb, 2025-04-18:
Hello, do you plan to setup a mounted camera support in the future as it is already possible with the original gripper ? Thank you in advance

augustin-crampette, 2025-04-22:
I have already made one quickly and a bit overengineered for the realsense, but I plan to redesign it again since now I know the angle I need. I could take this opportunity to make a support for the cameras suggested on the SO-100 Github.
Thanks for the input, now it's in my todo list :)

zuoxingdong, 2025-06-19:
@augustin-crampette Would you like to support webcam mount also?
e.g. logitech webcam

the problem with 32x32 cam module is that, I found the cable is very fragile after using for a while, due to frequent movement, the connection parts can be broken easily

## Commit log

2025-03-10 Add all documentation and cad files.
    [Bottom_Plate.step, Bottom_Plate.stl, Cam.step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]
2025-03-10 Better picture on cover of the assembly guide.
2025-03-21 Fix assembly instructions according to issue #1
2025-03-27 Add "finger tip for better grip" post
2025-04-07 Fix pin length mistake in the assembly instructions
2026-06-16 Add camera mount assembly guide

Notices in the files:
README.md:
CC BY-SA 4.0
